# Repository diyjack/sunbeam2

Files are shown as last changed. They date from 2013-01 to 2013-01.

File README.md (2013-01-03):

##Sunbeam2.0
==========

##What is it?
Just a smoothieboard based electronics that im developing.

## Licensing
==========

Copyright (C) 2012 Arkadiusz Spiewak (Wulfnor)

licensed under the GPL license: [http://www.gnu.org/licenses/gpl.html](http://www.gnu.org/licenses/gpl.html)
license.txt file included.

##Author
Author is: Arkadiusz Spiewak a'ka Wulfnor

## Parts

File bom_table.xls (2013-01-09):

Count | Value | Package | Manufacturer number | Digikey number | Notes | Parts | Digikey link | Farnel
1 | 74LVC1G04 | SOT-353 | SN74LVC1G04DCKR | 296-11600-1-ND |  | U4 | http://www.digikey.com/product-detail/en/SN74LVC1G04DCKR/296-11600-1-ND/385739
5 | 100uF | CPOL-EUUD-6,3X7,7 | EEE-1VA101XP | PCE3951CT-ND | >=35V | C23, C33, C40, C47, C54 | http://www.digikey.com/product-detail/en/EEE-1VA101XP/PCE3951CT-ND/766327
3 | FERRITE | FERRITE_0603 | MMZ1608S601A | 445-1549-1-ND |  | FB1, FB2, FB3 | http://www.digikey.com/product-detail/en/MMZ1608S601A/445-1549-1-ND/571879
1 | 39nH | INDUCTOR0603 | 1-1624109-1 | A102551CT-ND |  | L2 | http://www.digikey.com/product-detail/en/1-1624109-1/A102551CT-ND/2728577
1 | LAN8720 | 24-VFQFN | LAN8720A-CP | 638-1080-ND |  | U3 | http://www.digikey.com/product-detail/en/LAN8720A-CP/638-1080-ND/2051556
4 | Red | LEDCHIPLED_0805 | APT2012EC | 754-1128-1-ND |  | LED6, LED7, LED8, RX | http://www.digikey.com/product-detail/en/APT2012EC/754-1128-1-ND/1747845
3 | Green | LEDCHIPLED_0805 | APT2012SGC | 754-1131-1-ND |  | 3V3, +5V, TX | http://www.digikey.com/product-detail/en/APT2012SGC/754-1131-1-ND/1747848
3 | Blue | LEDCHIPLED_0805 | APHCM2012QBC/D-F01 | 754-1505-1-ND |  | LED2, LED3, LED4 | http://www.digikey.com/product-detail/en/APHCM2012QBC%2FD-F01/754-1505-1-ND/2263579
1 | LPC1769 | 100-LQFP | LPC1769FBD100,551 | 568-4966-ND |  | LPC1769 | http://www.digikey.com/product-search/en/integrated-circuits-ics/embedded-microcontrollers/2556109?k=LPC1769
1 | IRLML2246TRPBF | SOT-23 | IRLML2246TRPBF | IRLML2246TRPBFCT-ND |  | T1 | http://www.digikey.com/product-detail/en/IRLML2246TRPBF/IRLML2246TRPBFCT-ND/2639576
3 |  | SWITCH_TACT_SMT | MJTP1140TR | 679-2328-1-ND |  | PLAY, PROGRAM, RESET | http://www.digikey.com/product-detail/en/MJTP1140TR/679-2328-1-ND/2344141
5 | .22uF | C-EUC0603 | C1608X7R1A224K | 445-5132-1-ND |  | C16, C24, C34, C41, C48 | http://www.digikey.com/product-detail/en/C1608X7R1A224K/445-5132-1-ND/2093747
24 | 0.1uF | C-EUC0603 | C1608X7R1E104K080AA | 445-1316-1-ND |  | C3, C4, C5, C6, C7, C8, C9, C10, C17, C19, C29, C36, C43, C50, C55, C57, C58, C59, C63, C72, C79, C82, C83, C84 | http://www.digikey.com/product-detail/en/C1608X7R1E104K080AA/445-1316-1-ND/567697
16 | 0.1uF | C-EUC0805 | C2012X7R1H104K085AA | 445-7534-1-ND |  | C15, C20, C21, C22, C30, C31, C32, C37, C38, C39, C44, C45, C46, C51, C52, C53 | http://www.digikey.com/product-detail/en/C2012X7R1H104K085AA/445-7534-1-ND/2733606
10 | 0.5R | R-EU_R2512 | MCS3264R050FER | MCS3264R050FERCT-ND | 2W, 1% | R12, R13, R29, R30, R37, R38, R45, R46, R53, R54 | http://www.digikey.com/product-detail/en/MCS3264R050FER/MCS3264R050FERCT-ND/2003884
5 | 1K | R-EU_R0603 | ERJ-3GEYJ102V | P1.0KGCT-ND |  | R4, R74, R75, R82, R91 | http://www.digikey.com/product-detail/en/ERJ-3GEYJ102V/P1.0KGCT-ND/134874
9 | 1K5 | R-EU_R0603 | ERJ-3GEYJ152V | P1.5KGCT-ND |  | R17, R19, R21, R57, R63, R73, R94, R95, R96 | http://www.digikey.com/product-detail/en/ERJ-3GEYJ152V/P1.5KGCT-ND/134974
1 | 1M | R-EU_R0603 | ERJ-3GEYJ105V | P1.0MGCT-ND |  | R62 | http://www.digikey.com/product-detail/en/ERJ-3GEYJ105V/P1.0MGCT-ND/134885
7 | 1uF | C-EUC0603 | C1608X5R0J105K | 445-1322-1-ND |  | C18, C28, C35, C42, C49, C70, C71 | http://www.digikey.com/product-detail/en/C1608X5R0J105K/445-1322-1-ND/567695
1 | 1uF | CAP_POL1206 | F931C105MAA | 493-2364-1-ND |  | C60 | http://www.digikey.com/product-detail/en/F931C105MAA/493-2364-1-ND/677832
2 | 4.7uF | C-EUC0603 | C1608Y5V0J475Z | 445-3449-1-ND |  | C85, C86 | http://www.digikey.com/product-detail/en/C1608Y5V0J475Z/445-3449-1-ND/1801548
4 | 4K7 | R-EU_R0603 | ERJ-3GEYJ472V | P4.7KGCT-ND |  | R22, R23, R24,R90 | http://www.digikey.com/product-detail/en/ERJ-3GEYJ472V/P4.7KGCT-ND/135199
46 | 10K | R-EU_R0603 | ERJ-3GEYJ103V | P10KGCT-ND |  | R5, R6, R7, R8, R9, R10, R14, R15, R16, R18, R20, R25, R26, R27, R31, R32, R33, R34, R35, R39, R40, R41, R42, R43, R47, R48, R49, R50, R51, R55, R56, R58, R70, R71, R72, R77, R79, R81, R83, R88, R89,R11, R28, R36, R44, R52 | http://www.digikey.com/product-detail/en/ERJ-3GEYJ103V/P10KGCT-ND/134717
1 | 10nF | C-EUC0805 | C2012X7R1H103K | 445-1348-1-ND |  | C77 | http://www.digikey.com/product-detail/en/C2012X7R1H103K/445-1348-1-ND/567641
3 | 10uF | C-EUC0603 | C1608X5R0J106M080AB | 445-4112-1-ND |  | C25, C26, C27 | http://www.digikey.com/product-detail/en/C1608X5R0J106M080AB/445-4112-1-ND/1975462
5 | 10uF | CAP_POL1206 | F931A106MAA | 493-2351-1-ND |  | C11, C14, C56, C61, C73 | http://www.digikey.com/product-detail/en/F931A106MAA/493-2351-1-ND/677819
1 | 12Mhz | CRYSTAL2734 | 403C35D12M00000 | CTX839CT-ND |  | U$3 | http://www.digikey.com/product-detail/en/403C35D12M00000/CTX839CT-ND/2293004
10 | 18pF | C-EUC0603 | C1608C0G1H180J080AA | 445-1272-1-ND |  | C1, C2, C12, C13, C64, C65, C66, C67, C68, C69 | http://www.digikey.com/product-detail/en/C1608C0G1H180J080AA/445-1272-1-ND/567674
6 | 22-23-2021 | 22-23-2021 | 22272021 | WM4111-ND |  | FAN1, FAN2, FAN3, T_E0, T_E1, T_HB | http://www.digikey.com/product-detail/en/0022272021/WM4111-ND/1130577
6 | 22-23-2031 | 22-23-2031 | 22272031 | WM4112-ND |  | X_MAX, X_MIN, Y_MAX, Y_MIN, Z_MAX, Z_MIN | http://www.digikey.com/product-detail/en/0022272031/WM4112-ND/1130578
5 | 22-23-2041 | 22-23-2041 | 22272041 | WM4113-ND |  | E0_AXIS, E1_AXIS, X_AXIS, Y_AXIS, Z_AXIS | http://www.digikey.com/product-detail/en/0022272041/WM4113-ND/1130579
6 | 22R | R-EU_R0603 | ERJ-3GEYJ220V | P22GCT-ND |  | R59, R60, R61, R76, R78, R80 | http://www.digikey.com/product-detail/en/ERJ-3GEYJ220V/P22GCT-ND/134662
1 | 25Mhz | CRYSTAL2734 | 403C35D25M00000 | CTX953CT-ND |  | U$8 | http://www.digikey.com/product-detail/en/403C35D25M00000/CTX953CT-ND/2640300
2 | 33R | R-EU_R0603 | ERJ-3GEYJ330V | P33GCT-ND |  | R1, R2 | http://www.digikey.com/product-detail/en/ERJ-3GEYJ330V/P33GCT-ND/134674
1 | 33uH | L-EUPIS2816 | 46333C | 811-1177-1-ND |  | L4 | http://www.digikey.com/product-detail/en/46333C/811-1177-1-ND/1924937
1 | 47uF | CAP_TANTALUMD/7343_REFLOW | TPSD476K016R0150 | 478-1788-1-ND |  | C76 | http://www.digikey.com/product-detail/en/TPSD476K016R0150/478-1788-1-ND/564820
4 | 49.9R | R-EU_R0603 | ERJ-3EKF49R9V | P49.9HCT-ND |  | R64, R65, R66, R67 | http://www.digikey.com/product-detail/en/ERJ-3EKF49R9V/P49.9HCT-ND/198412
1 | 470R | R-EU_R0603 | ERJ-3GEYJ471V | P470GCT-ND |  | R3 | http://www.digikey.com/product-detail/en/ERJ-3GEYJ471V/P470GCT-ND/134802
1 | 100uF | CPOL-EUUD-8X10 | EEE-FP1V101AP | PCE4442CT-ND |  | C78 | http://www.digikey.com/product-detail/en/EEE-FP1V101AP/PCE4442CT-ND/1246022
1 | 220uF | CPOL-EUUD-8X10 | ECE-V1AA221P | PCE2040CT-ND |  | C74 | http://www.digikey.com/product-detail/en/ECE-V1AA221P/PCE2040CT-ND/204211
2 | 330R | R-EU_R0603 | ERJ-3GEYJ331V | P330GCT-ND |  | R68, R69 | http://www.digikey.com/product-detail/en/ERJ-3GEYJ331V/P330GCT-ND/134778
1 | 470nF | C-EUC0805 | C2012Y5V1H474Z/0.85 | 445-7681-1-ND |  | C75 | http://www.digikey.com/product-detail/en/C2012Y5V1H474Z%2F0.85/445-7681-1-ND/2733753
1 | 470pF | C-EUC0603 | C1608X7R1H471K | 445-1307-1-ND |  | C62 | http://www.digikey.com/product-detail/en/C1608X7R1H471K/445-1307-1-ND/567709
2 | 500mA | L-EUL1812 | 0ZCC0050FF2C | 507-1361-1-ND |  | F1, F2 | http://www.digikey.com/product-detail/en/0ZCC0050FF2C/507-1361-1-ND/1560228
1 | 2520- | 2520- | 30320-6002HB | 3M11932-ND |  | PANEL | http://www.digikey.com/product-detail/en/30320-6002HB/3M11932-ND/1237399
5 | A4988 | 28-VFQFN | A4988SETTR-T | 620-1343-1-ND |  | IC2, IC3, IC4, IC5, IC6 | http://www.digikey.com/product-detail/en/A4988SETTR-T/620-1343-1-ND/2238004
1 | AD5206 | 24-TSSOP | AD5206BRUZ10-RL7 | AD5206BRUZ10-RL7CT-ND |  | AD5206 | http://www.digikey.com/product-detail/en/AD5206BRUZ10-RL7/AD5206BRUZ10-RL7CT-ND/3727008
1 | BC857ALT1SMD | SOT-23 | BC857A,215 | 568-6082-1-ND |  | Q1 | http://www.digikey.com/product-detail/en/BC857A,215/568-6082-1-ND/2531369
5 | Extruder0 | W237-102 | 1776244-2 | A97996-ND |  | E0, E1, HB, V_HEAT, V_MOT | http://www.digikey.com/product-detail/en/1776244-2/A97996-ND/1826859
1 | FT232RLSSOP | 28-SSOP | FT232RL-REEL | 768-1007-1-ND |  | IC7 | http://www.digikey.com/product-detail/en/FT232RL-REEL/768-1007-1-ND/1836402
1 | J0011D21B | J0011D21B | J0011D21BNL | 553-1485-ND |  | RJ1 | http://www.digikey.com/scripts/dksearch/dksus.dll?vendor=0&keywords=J0011D21B
3 | IRLHM630TR2PBF | PQFN (3x3) | RLHM630TR2PBF | IRLHM630TR2PBFCT-ND |  | Q2, Q3, Q4 | http://www.digikey.com/product-detail/en/IRLHM630TR2PBF/IRLHM630TR2PBFCT-ND/2464888
3 | IRLR8743 | D-Pak | IRLR8743TRPBF | IRLR8743TRPBFCT-ND |  | E0_FET, E1_FET, HOTBET_FET | http://www.digikey.com/product-detail/en/IRLR8743TRPBF/IRLR8743TRPBFCT-ND/1925566
1 | LM1117IMPX-3.3 | SOT-223-3 | LM1117MPX-3.3/NOPB | LM1117MPX-3.3/NOPBCT-ND |  | IC10 | http://www.digikey.com/product-detail/en/LM1117MPX-3.3%2FNOPB/LM1117MPX-3.3%2FNOPBCT-ND/1010516
1 | LM2675 | 8-SOIC | LM2675M-5.0/NOPB | LM2675M-5.0/NOPB-ND |  | IC8 | http://www.digikey.com/product-detail/en/LM2675M-5.0%2FNOPB/LM2675M-5.0%2FNOPB-ND/271162
1 | LMV358MMX | 8-MSOP | LMV358MM/NOPB | LMV358MM/NOPBCT-ND |  | IC9 | http://www.digikey.com/product-detail/en/LMV358MM%2FNOPB/LMV358MM%2FNOPBCT-ND/270768
2 | M4 | DIODE-DO214AC | S1G-E3/5AT | S1G-E3/5ATGICT-ND |  | D2, D3 | http://www.digikey.com/product-detail/en/S1G-E3%2F5AT/S1G-E3%2F5ATGICT-ND/3025911
2 | SMF_OMNIBLOK_154.062 | SMF_OMNIBLOK_154.062 | 0154007.DR | F1229CT-ND |  | F3 | http://www.digikey.com/product-detail/en/0154007.DR/F1229CT-ND/565517
1 | 01530008Z | 01530008Z | 01530008Z | F065-ND |  | F4 | http://www.digikey.com/product-detail/en/01530008Z/F065-ND/183334
1 | SS14 | DIODE-DO214AC | SS14-E3/61T | SS14-E3/61TGICT-ND |  | D1 | http://www.digikey.com/product-detail/en/SS14-E3%2F61T/SS14-E3%2F61TGICT-ND/1091668
2 | TC4427 | 8-SOIC | TC4427ACOA713 | TC4427ACOA713CT-ND |  | FET_DRV1, FET_DRV2 | http://www.digikey.com/product-detail/en/TC4427ACOA713/TC4427ACOA713CT-ND/3622383
1 | USB+SHIELD | USB+SHIELD | 670689000 | WM17131-ND |  | U$1 | http://www.digikey.com/product-detail/en/0670689000/WM17131-ND/755221
1 | USB-MINIB-5PIN | USB-MINIB-5PIN | 675031020 | WM5461CT-ND |  | U$7 | http://www.digikey.com/product-detail/en/0675031020/WM5461CT-ND/1624427
1 | USD-SOCKETNEW | USD-SOCKETNEW | 101-00660-68-6 | 101-00660-68-6-1-ND |  | U2 | http://www.digikey.com/product-detail/en/101-00660-68-6/101-00660-68-6-1-ND/2187099
2 | VARISTORCN0603 | VARISTORCN0603 | B72500D50A60 | 495-3414-1-ND |  | R97, R98 | http://www.digikey.com/product-detail/en/B72500D50A60/495-3414-1-ND/1589665

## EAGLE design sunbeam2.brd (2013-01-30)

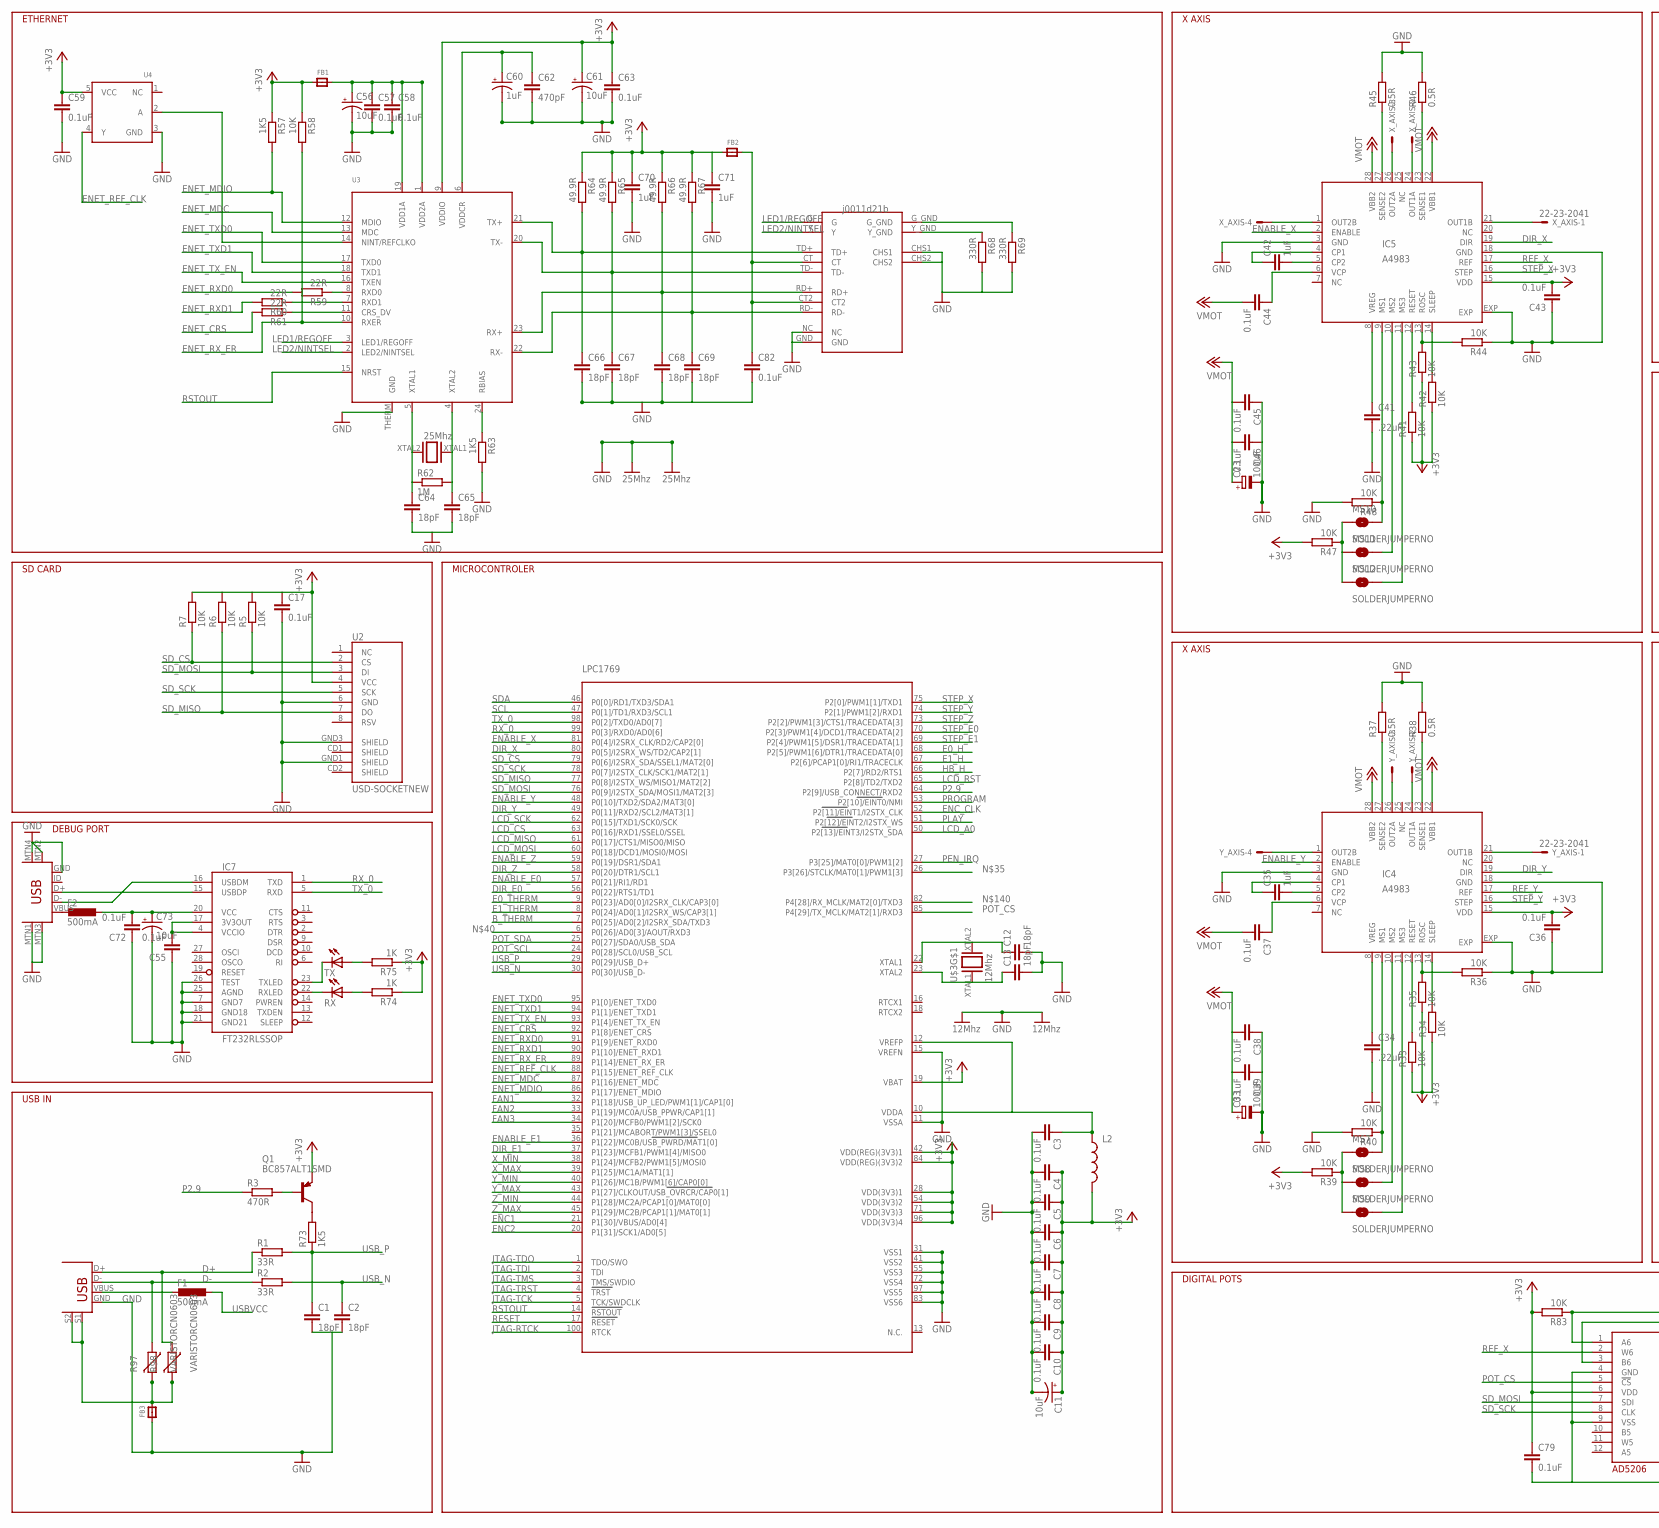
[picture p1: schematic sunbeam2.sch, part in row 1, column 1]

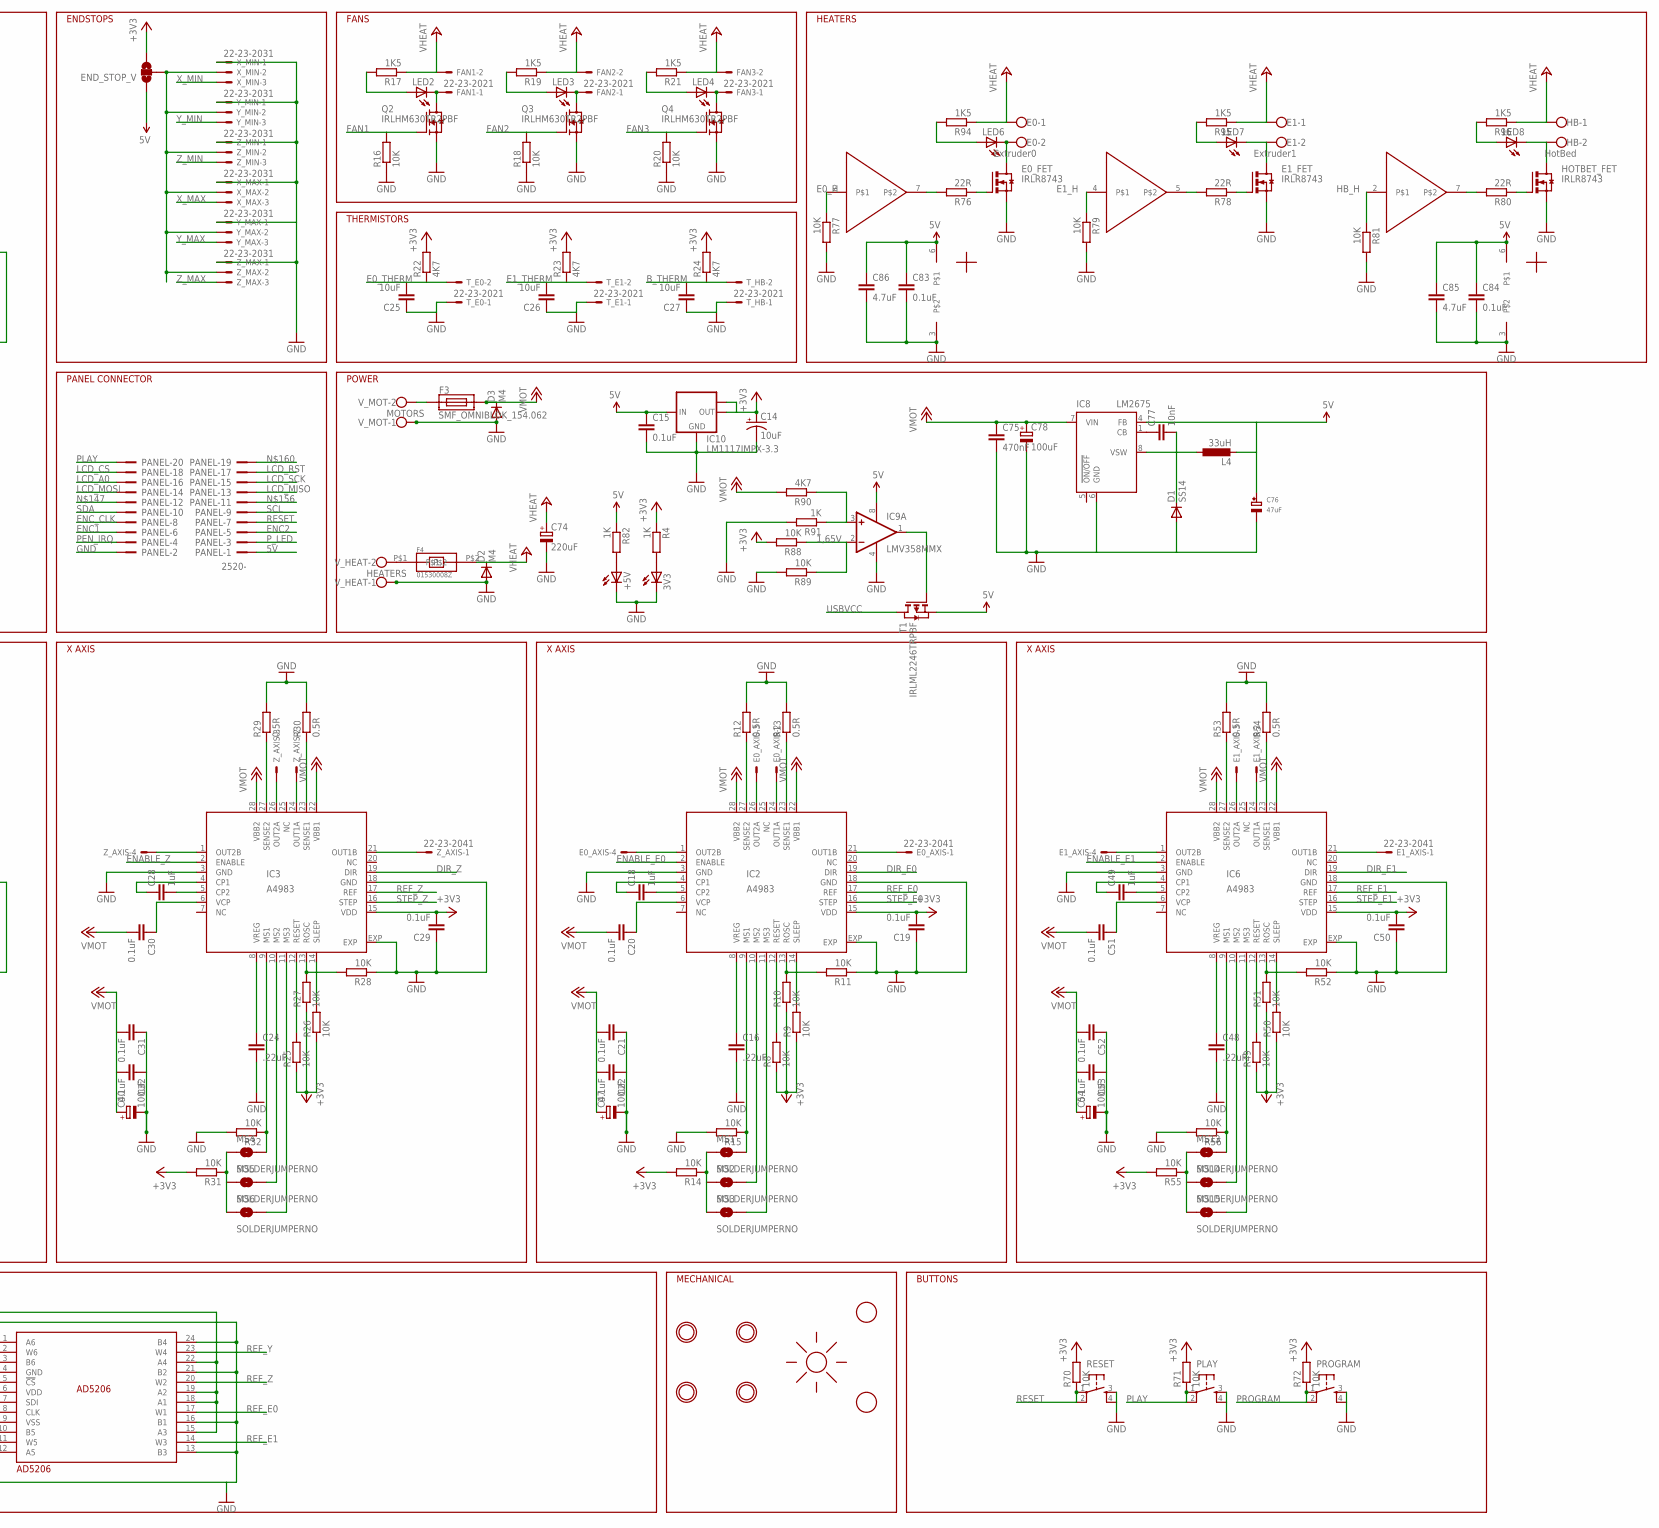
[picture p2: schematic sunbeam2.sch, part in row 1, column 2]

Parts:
3V3: LEDCHIPLED_0805; CHIPLED_0805
+5V: LEDCHIPLED_0805; CHIPLED_0805
AD5206: AD5206; TSSOP24
C1, C2, C12, C13, C64, C65, C66, C67, C68, C69: 18pF; C0603
C3, C4, C5, C6, C7, C8, C9, C10, C17, C19, C29, C36, C43, C50, C55, C57, C58, C59, C63, C72, C79, C82, C83, C84: 0.1uF; C0603
C11, C14, C56, C61, C73: 10uF; EIA3216
C15, C20, C21, C22, C30, C31, C32, C37, C38, C39, C44, C45, C46, C51, C52, C53: 0.1uF; C0805
C16, C24, C34, C41, C48: .22uF; C0603
C18, C28, C35, C42, C49, C70, C71: 1uF; C0603
C23, C33, C40, C47, C54: 100uF; UD-6,3X7,7_NICHICON
C25, C26, C27: 10uF; C0603
C60: 1uF; EIA3216
C62: 470pF; C0603
C74: 220uF; UD-8X10_NICHICON
C75: 470nF; C0805
C76: 47uF; EIA7343-31/D-R
C77: 10nF; C0805
C78: 100uF; UD-8X10_NICHICON
C85, C86: 4.7uF; C0603
D1: SS14; DO214AC
D2, D3: M4; DO214AC
E0: Extruder0; W237-102; MPN 237-102
E0_AXIS, E1_AXIS: 22-23-2041
E0_FET, E1_FET: IRLR8743; D-PAK_TO252AA
E1: Extruder1; W237-102; MPN 237-102
END_STOP_V: SOLDERJUMPER_2WAYS; SJ_3
F1, F2: 500mA; L1812
F3: SMF_OMNIBLOK_154.062; NANO2_SMF_FUSEBLOCK
F4: 01530008Z
FAN1, FAN2, FAN3: 22-23-2021
FB1, FB2, FB3: FERRITE_0603; _0603
FET_DRV1, FET_DRV2: TC4427; SOIC8
GND: MOUNTINGHOLE3.0THIN; MOUNTINGHOLE_3.0_PLATEDTHIN
HB: HotBed; W237-102; MPN 237-102
HOTBET_FET: IRLR8743; D-PAK_TO252AA
IC2, IC3, IC4, IC5, IC6: A4983; QFN28ET
IC7: FT232RLSSOP; SSOP28DB
IC8: LM2675; SO08
IC9: LMV358MMX; MSOP08
IC10: LM1117IMPX-3.3; SOT223
L2: INDUCTOR0603; 0603
L4: 33uH; PIS2816
LED2, LED3, LED4, LED6, LED7, LED8: LEDCHIPLED_0805; CHIPLED_0805
LPC1769: LPC1768; LQFP100
MS1, MS2, MS3, MS4, MS5, MS6, MS7, MS8, MS9, MS10, MS11, MS12, MS13, MS14, MS15: SOLDERJUMPERNO; SJ_2S-NO
PANEL: 2520-; PAK100/2500-20
PLAY: TAC_SWITCHSMD; TACTILE_SWITCH_SMD
PROGRAM: TAC_SWITCHSMD; TACTILE_SWITCH_SMD
Q1: BC857ALT1SMD; SOT23-BEC
Q2, Q3, Q4: IRLHM630TR2PBF; PQFN33
R1, R2: 33R; R0603
R3: 470R; R0603
R4, R74, R75, R82, R91: 1K; R0603
R5, R6, R7, R8, R9, R10, R11, R14, R15, R16, R18, R20, R25, R26, R27, R28, R31, R32, R33, R34, R35, R36, R39, R40, R41, R42, R43, R44, R47, R48, R49, R50, R51, R52, R55, R56, R58, R70, R71, R72, R77, R79, R81, R83, R88, R89: 10K; R0603
R12, R13, R29, R30, R37, R38, R45, R46, R53, R54: 0.5R; R2512
R17, R19, R21, R57, R63, R73, R94, R95, R96: 1K5; R0603
R22, R23, R24, R90: 4K7; R0603
R59, R60, R61, R76, R78, R80: 22R; R0603
R62: 1M; R0603
R64, R65, R66, R67: 49.9R; R0603
R68, R69: 330R; R0603
R97, R98: VARISTORCN0603; CT/CN0603
RESET: TAC_SWITCHSMD; TACTILE_SWITCH_SMD
RJ1: ETHERNET; J0011D21B
RX: LEDCHIPLED_0805; CHIPLED_0805
T1: IRLML2246TRPBF; SOT-23
TX: LEDCHIPLED_0805; CHIPLED_0805
T_E0, T_E1: 22-23-2021
T_HB: 22-23-2021
U2: USD-SOCKETNEW; MICRO-SD-SOCKET-PP
U3: LAN8720; QFN24_4MM
U4: 74LVC1G04; SOT23-5
U$1: USB+SHIELD; USB-B-PTH
U$3: 12Mhz; CRYSTAL2734
U$7: USB-MINIB-5PIN; USB-MINIB
U$8: 25Mhz; CRYSTAL2734
U$17, U$18, U$20: MOUNTINGHOLE3.0THIN; MOUNTINGHOLE_3.0_PLATEDTHIN
U$21: SUNLOGO; SUN
U$22, U$23: FIDUCIAL; FIDUCIAL_1MM
V_HEAT: HEATERS; W237-102
V_MOT: MOTORS; W237-102
X_AXIS: 22-23-2041
X_MAX: 22-23-2031; MPN 22-23-2031
X_MIN: 22-23-2031
Y_AXIS: 22-23-2041
Y_MAX: 22-23-2031; MPN 22-23-2031
Y_MIN: 22-23-2031
Z_AXIS: 22-23-2041
Z_MAX: 22-23-2031; MPN 22-23-2031
Z_MIN: 22-23-2031

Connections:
1,65V: IC9.2 (-IN), R88.1, R89.1
5V: C15.1, C76.+, C83.1, C84.1, C85.1, C86.1, END_STOP_V.1, FET_DRV1.6, FET_DRV2.6, IC8.4 (FB), IC9.8 (V+), IC10.3 (IN), L4.2, PANEL.1, R82.1, T1.2 (S)
+3V3: AD5206.6 (VDD), C4.1, C5.1, C6.1, C7.1, C8.1, C9.1, C10.1, C11.A (+), C14.A (+), C17.1, C19.2, C29.2, C36.2, C43.2, C50.2, C59.1, C61.A (+), C63.1, C70.1, C71.1, C79.1, END_STOP_V.3, FB1.1, FB2.1, IC2.15 (VDD), IC3.15 (VDD), IC4.15 (VDD), IC5.15 (VDD), IC6.15 (VDD), IC10.2 (OUT), IC10.TAB (OUT1), L2.2, LPC1769.19 (VBAT), LPC1769.28 (VDD(3V3)1), LPC1769.42 (VDD(REG)(3V3)1), LPC1769.54 (VDD(3V3)2), LPC1769.71 (VDD(3V3)3), LPC1769.84 (VDD(REG)(3V3)2), LPC1769.96 (VDD(3V3)4), Q1.E, R4.1, R5.2, R6.2, R7.2, R8.1, R9.1, R10.1, R14.2, R22.2, R23.2, R24.2, R25.1, R26.1, R27.1, R31.2, R33.1, R34.1, R35.1, R39.2, R41.1, R42.1, R43.1, R47.2, R49.1, R50.1, R51.1, R55.2, R57.1, R58.1, R64.1, R65.1, R66.1, R67.1, R70.2, R71.2, R72.2, R74.1, R75.1, R83.2, R88.2, U2.4 (VCC), U3.9 (VDDIO), U4.5 (VCC)
+12V: C20.2, C21.2, C22.2, C23.+, C30.2, C31.2, C32.2, C33.+, C37.2, C38.2, C39.2, C40.+, C44.2, C45.2, C46.2, C47.+, C51.2, C52.2, C53.2, C54.+, C75.1, C78.+, D3.C, F3.2, IC2.22 (VBB1), IC2.28 (VBB2), IC3.22 (VBB1), IC3.28 (VBB2), IC4.22 (VBB1), IC4.28 (VBB2), IC5.22 (VBB1), IC5.28 (VBB2), IC6.22 (VBB1), IC6.28 (VBB2), IC8.7 (VIN), R90.2
B_THERM: C27.2, LPC1769.7 (P0[25]/AD0[2]/I2SRX_SDA/TXD3), R24.1, T_HB.2
D+: R1.1, R98.1, U$1.D+
D-: R2.1, R97.1, U$1.D-
DIR_E0: IC2.19 (DIR), LPC1769.56 (P0[22]/RTS1/TD1)
DIR_E1: IC6.19 (DIR), LPC1769.37 (P1[23]/MCFB1/PWM1[4]/MISO0)
DIR_X: IC5.19 (DIR), LPC1769.80 (P0[5]/I2SRX_WS/TD2/CAP2[1])
DIR_Y: IC4.19 (DIR), LPC1769.49 (P0[11]/RXD2/SCL2/MAT3[1])
DIR_Z: IC3.19 (DIR), LPC1769.58 (P0[20]/DTR1/SCL1)
E0_H: FET_DRV1.2, LPC1769.68 (P2[5]/PWM1[6]/DTR1/TRACEDATA[0]), R77.1
E0_THERM: C25.2, LPC1769.9 (P0[23]/AD0[0]/I2SRX_CLK/CAP3[0]), R22.1, T_E0.2
E1_H: FET_DRV1.4, LPC1769.67 (P2[6]/PCAP1[0]/RI1/TRACECLK), R79.1
E1_THERM: C26.2, LPC1769.8 (P0[24]/AD0[1]/I2SRX_WS/CAP3[1]), R23.1, T_E1.2
ENABLE_E0: IC2.2 (ENABLE), LPC1769.57 (P0[21]/RI1/RD1)
ENABLE_E1: IC6.2 (ENABLE), LPC1769.36 (P1[22]/MC0B/USB_PWRD/MAT1[0])
ENABLE_X: IC5.2 (ENABLE), LPC1769.81 (P0[4]/I2SRX_CLK/RD2/CAP2[0])
ENABLE_Y: IC4.2 (ENABLE), LPC1769.48 (P0[10]/TXD2/SDA2/MAT3[0])
ENABLE_Z: IC3.2 (ENABLE), LPC1769.59 (P0[19]/DSR1/SDA1)
ENC1: LPC1769.21 (P1[30]/VBUS/AD0[4]), PANEL.6
ENC2: LPC1769.20 (P1[31]/SCK1/AD0[5]), PANEL.5
ENC_CLK: LPC1769.52 (P2[11]/EINT1/I2STX_CLK), PANEL.8
ENET_CRS: LPC1769.92 (P1[8]/ENET_CRS), R61.2
ENET_MDC: LPC1769.87 (P1[16]/ENET_MDC), U3.13 (MDC)
ENET_MDIO: LPC1769.86 (P1[17]/ENET_MDIO), R57.2, U3.12 (MDIO)
ENET_REF_CLK: LPC1769.88 (P1[15]/ENET_REF_CLK), U4.4 (Y)
ENET_RXD0: LPC1769.91 (P1[9]/ENET_RXD0), R59.2
ENET_RXD1: LPC1769.90 (P1[10]/ENET_RXD1), R60.2
ENET_RX_ER: LPC1769.89 (P1[14]/ENET_RX_ER), R58.2, U3.10 (RXER)
ENET_TXD0: LPC1769.95 (P1[0]/ENET_TXD0), U3.17 (TXD0)
ENET_TXD1: LPC1769.94 (P1[1]/ENET_TXD1), U3.18 (TXD1)
ENET_TX_EN: LPC1769.93 (P1[4]/ENET_TX_EN), U3.16 (TXEN)
FAN1: LPC1769.32 (P1[18]/USB_UP_LED/PWM1[1]/CAP1[0]), Q2.G, R16.2
FAN2: LPC1769.33 (P1[19]/MC0A/USB_PPWR/CAP1[1]), Q3.G, R18.2
FAN3: LPC1769.34 (P1[20]/MCFB0/PWM1[2]/SCK0), Q4.G, R20.2
GND: 3V3.C, +5V.C, AD5206.3 (B6), AD5206.4 (GND), AD5206.9 (VSS), AD5206.13 (B3), AD5206.16 (B1), AD5206.21 (B2), AD5206.24 (B4), C1.2, C2.2, C3.2, C4.2, C5.2, C6.2, C7.2, C8.2, C9.2, C10.2, C11.C (-), C12.2, C13.2, C14.C (-), C15.2, C16.2, C17.2, C19.1, C21.1, C22.1, C23.-, C24.2, C25.1, C26.1, C27.1, C29.1, C31.1, C32.1, C33.-, C34.2, C36.1, C38.1, C39.1, C40.-, C41.2, C43.1, C45.1, C46.1, C47.-, C48.2, C50.1, C52.1, C53.1, C54.-, C55.1, C56.C (-), C57.2, C58.2, C59.2, C60.C (-), C61.C (-), C62.2, C63.2, C64.2, C65.2, C66.2, C67.2, C68.2, C69.2, C70.2, C71.2, C72.1, C73.C (-), C74.-, C75.2, C76.-, C78.-, C79.2, C82.2, C83.2, C84.2, C85.2, C86.2, D1.A, D2.A, D3.A, E0_FET.3 (S), E1_FET.3 (S), FB3.1, FET_DRV1.3, FET_DRV2.3, HOTBET_FET.3 (S), IC2.3 (GND), IC2.18 (GND), IC2.EXP, IC3.3 (GND), IC3.18 (GND), IC3.EXP, IC4.3 (GND), IC4.18 (GND), IC4.EXP, IC5.3 (GND), IC5.18 (GND), IC5.EXP, IC6.3 (GND), IC6.18 (GND), IC6.EXP, IC7.7 (GND7), IC7.18 (GND18), IC7.21 (GND21), IC7.25 (AGND), IC7.26 (TEST), IC8.6 (GND), IC9.4 (V-), IC10.1 (GND), LPC1769.11 (VSSA), LPC1769.15 (VREFN), LPC1769.31 (VSS1), LPC1769.41 (VSS2), LPC1769.55 (VSS3), LPC1769.72 (VSS4), LPC1769.83 (VSS6), LPC1769.97 (VSS5), PANEL.2, PLAY.3, PLAY.4, PROGRAM.3, PROGRAM.4, Q2.S, Q3.S, Q4.S, R11.1, R12.2, R13.2, R15.2, R16.1, R18.1, R20.1, R28.1, R29.2, R30.2, R32.2, R36.1, R37.2, R38.2, R40.2, R44.1, R45.2, R46.2, R48.2, R52.1, R53.2, R54.2, R56.2, R63.2, R68.2, R69.2, R77.2, R79.2, R81.2, R89.2, R91.2, RESET.3, RESET.4, RJ1.CHS1, RJ1.CHS2, RJ1.GND, RJ1.NC, T_E0.1, T_E1.1, T_HB.1, U2.6 (GND), U2.GND1 (SHIELD), U2.GND3 (SHIELD), U3.THERM (GND), U4.3 (GND), U$1.GND, U$3.GND1 (GND), U$3.GND2 (GND), U$7.GND, U$7.MTN1 (MTN2), U$7.MTN2 (MTN3), U$7.MTN3 (MTN1), U$7.MTN4, U$8.GND1 (GND), U$8.GND2 (GND), V_HEAT.1, V_MOT.1, X_MAX.1, X_MIN.1, Y_MAX.1, Y_MIN.1, Z_MAX.1, Z_MIN.1
HB_H: FET_DRV2.2, LPC1769.66 (P2[7]/RD2/RTS1), R81.1
JTAG-RTCK: LPC1769.100 (RTCK)
JTAG-TCK: LPC1769.5 (TCK/SWDCLK)
JTAG-TDI: LPC1769.2 (TDI)
JTAG-TDO: LPC1769.1 (TDO/SWO)
JTAG-TMS: LPC1769.3 (TMS/SWDIO)
JTAG-TRST: LPC1769.4 (TRST)
LCD_A0: LPC1769.50 (P2[13]/EINT3/I2STX_SDA), PANEL.16
LCD_CS: LPC1769.63 (P0[16]/RXD1/SSEL0/SSEL), PANEL.18
LCD_MISO: LPC1769.61 (P0[17]/CTS1/MISO0/MISO), PANEL.13
LCD_MOSI: LPC1769.60 (P0[18]/DCD1/MOSI0/MOSI), PANEL.14
LCD_RST: LPC1769.65 (P2[8]/TD2/TXD2), PANEL.17
LCD_SCK: LPC1769.62 (P0[15]/TXD1/SCK0/SCK), PANEL.15
LED1/REGOFF: RJ1.G, U3.3 (LED1/REGOFF)
LED2/NINTSEL: RJ1.Y, U3.2 (LED2/NINTSEL)
unnamed: F1.2, U$1.VBUS
unnamed: Q1.B, R3.2
unnamed: FB3.2, R97.2, R98.2, U$1.S1, U$1.S2
unnamed: FAN1.1, LED2.C, Q2.D
unnamed: FAN2.1, LED3.C, Q3.D
unnamed: C13.1, LPC1769.23 (XTAL2), U$3.XTAL1 (1)
unnamed: C12.1, LPC1769.22 (XTAL1), U$3.XTAL2 (2)
unnamed: E0_AXIS.1, IC2.21 (OUT1B)
unnamed: E0_AXIS.2, IC2.24 (OUT1A)
unnamed: 3V3.A, R4.2
unnamed: C3.1, L2.1, LPC1769.10 (VDDA), LPC1769.12 (VREFP)
unnamed: E0_AXIS.3, IC2.26 (OUT2A)
unnamed: E0_AXIS.4, IC2.1 (OUT2B)
unnamed: IC2.12 (RESET), R8.2
unnamed: IC2.14 (SLEEP), R9.2
unnamed: IC2.13 (ROSC), R10.2, R11.2
unnamed: C16.1, IC2.8 (VREG)
unnamed: C18.2, IC2.5 (CP2)
unnamed: C18.1, IC2.4 (CP1)
unnamed: IC2.27 (SENSE2), R12.1
unnamed: IC2.23 (SENSE1), R13.1
unnamed: C20.1, IC2.6 (VCP)
unnamed: IC2.9 (MS1), MS1.2, R15.1
unnamed: IC2.10 (MS2), MS2.2
unnamed: IC2.11 (MS3), MS3.2
unnamed: MS1.1, MS2.1, MS3.1, R14.1
unnamed: F3.1, V_MOT.2
unnamed: HB.2, HOTBET_FET.4 (D), LED8.C
unnamed: E1.2, E1_FET.4 (D), LED7.C
unnamed: E0.2, E0_FET.4 (D), LED6.C
unnamed: E0_FET.1 (G), R76.1
unnamed: E1_FET.1 (G), R78.1
unnamed: FET_DRV1.7, R76.2
unnamed: LED6.A, R94.2
unnamed: Q1.C, R73.2
unnamed: IC3.21 (OUT1B), Z_AXIS.1
unnamed: IC3.24 (OUT1A), Z_AXIS.2
unnamed: IC3.26 (OUT2A), Z_AXIS.3
unnamed: IC3.1 (OUT2B), Z_AXIS.4
unnamed: LED3.A, R19.2
unnamed: END_STOP_V.2, X_MAX.2, X_MIN.2, Y_MAX.2, Y_MIN.2, Z_MAX.2, Z_MIN.2
unnamed: LED2.A, R17.2
unnamed: FAN3.1, LED4.C, Q4.D
unnamed: LED4.A, R21.2
unnamed: IC3.12 (RESET), R25.2
unnamed: IC3.14 (SLEEP), R26.2
unnamed: IC3.13 (ROSC), R27.2, R28.2
unnamed: C24.1, IC3.8 (VREG)
unnamed: C28.2, IC3.5 (CP2)
unnamed: C28.1, IC3.4 (CP1)
unnamed: IC3.27 (SENSE2), R29.1
unnamed: IC3.23 (SENSE1), R30.1
unnamed: C30.1, IC3.6 (VCP)
unnamed: IC3.9 (MS1), MS4.2, R32.1
unnamed: IC3.10 (MS2), MS5.2
unnamed: IC3.11 (MS3), MS6.2
unnamed: MS4.1, MS5.1, MS6.1, R31.1
unnamed: IC4.21 (OUT1B), Y_AXIS.1
unnamed: IC4.24 (OUT1A), Y_AXIS.2
unnamed: IC4.26 (OUT2A), Y_AXIS.3
unnamed: IC4.1 (OUT2B), Y_AXIS.4
unnamed: IC4.12 (RESET), R33.2
unnamed: IC4.14 (SLEEP), R34.2
unnamed: IC4.13 (ROSC), R35.2, R36.2
unnamed: C34.1, IC4.8 (VREG)
unnamed: C35.2, IC4.5 (CP2)
unnamed: C35.1, IC4.4 (CP1)
unnamed: IC4.27 (SENSE2), R37.1
unnamed: IC4.23 (SENSE1), R38.1
unnamed: C37.1, IC4.6 (VCP)
unnamed: IC4.9 (MS1), MS7.2, R40.1
unnamed: IC4.10 (MS2), MS8.2
unnamed: IC4.11 (MS3), MS9.2
unnamed: MS7.1, MS8.1, MS9.1, R39.1
unnamed: IC5.21 (OUT1B), X_AXIS.1
unnamed: IC5.24 (OUT1A), X_AXIS.2
unnamed: IC5.26 (OUT2A), X_AXIS.3
unnamed: IC5.1 (OUT2B), X_AXIS.4
unnamed: IC5.12 (RESET), R41.2
unnamed: IC5.14 (SLEEP), R42.2
unnamed: IC5.13 (ROSC), R43.2, R44.2
unnamed: C41.1, IC5.8 (VREG)
unnamed: C42.2, IC5.5 (CP2)
unnamed: C42.1, IC5.4 (CP1)
unnamed: IC5.27 (SENSE2), R45.1
unnamed: IC5.23 (SENSE1), R46.1
unnamed: C44.1, IC5.6 (VCP)
unnamed: IC5.9 (MS1), MS10.2, R48.1
unnamed: IC5.10 (MS2), MS11.2
unnamed: IC5.11 (MS3), MS12.2
unnamed: MS10.1, MS11.1, MS12.1, R47.1
unnamed: E1_AXIS.1, IC6.21 (OUT1B)
unnamed: E1_AXIS.2, IC6.24 (OUT1A)
unnamed: E1_AXIS.3, IC6.26 (OUT2A)
unnamed: E1_AXIS.4, IC6.1 (OUT2B)
unnamed: IC6.12 (RESET), R49.2
unnamed: IC6.14 (SLEEP), R50.2
unnamed: IC6.13 (ROSC), R51.2, R52.2
unnamed: C48.1, IC6.8 (VREG)
unnamed: C49.2, IC6.5 (CP2)
unnamed: C49.1, IC6.4 (CP1)
unnamed: IC6.27 (SENSE2), R53.1
unnamed: IC6.23 (SENSE1), R54.1
unnamed: C51.1, IC6.6 (VCP)
unnamed: IC6.9 (MS1), MS13.2, R56.1
unnamed: IC6.10 (MS2), MS14.2
unnamed: IC6.11 (MS3), MS15.2
unnamed: MS13.1, MS14.1, MS15.1, R55.1
unnamed: F2.2, U$7.VBUS
unnamed: IC7.15 (USBDP), U$7.D+
unnamed: IC7.16 (USBDM), U$7.D-
unnamed: C72.2, C73.A (+), F2.1, IC7.20 (VCC)
unnamed: C55.2, IC7.4 (VCCIO), IC7.17 (3V3OUT)
unnamed: IC7.22 (RXLED), RX.C
unnamed: F4.P$1, V_HEAT.2
unnamed: C56.A (+), C57.1, C58.1, FB1.2, U3.1 (VDD2A), U3.19 (VDD1A)
unnamed: R63.1, U3.24 (RBIAS)
unnamed: R74.2, RX.A
unnamed: U3.14 (NINT/REFCLKO), U4.2 (A)
unnamed: R59.1, U3.8 (RXD0)
unnamed: R60.1, U3.7 (RXD1)
unnamed: R61.1, U3.11 (CRS_DV)
unnamed: C65.1, R62.2, U3.4 (XTAL2), U$8.XTAL1 (1)
unnamed: C66.1, R64.2, RJ1.TD+, U3.21 (TX+)
unnamed: C60.A (+), C62.1, U3.6 (VDDCR)
unnamed: C64.1, R62.1, U3.5 (XTAL1), U$8.XTAL2 (2)
unnamed: C67.1, R65.2, RJ1.TD-, U3.20 (TX-)
unnamed: IC7.23 (TXLED), TX.C
unnamed: R75.2, TX.A
unnamed: FET_DRV1.5, R78.2
unnamed: C77.2, D1.C, IC8.8 (VSW), L4.1
unnamed: +5V.A, R82.2
unnamed: HOTBET_FET.1 (G), R80.1
unnamed: FET_DRV2.7, R80.2
unnamed: C69.1, R67.2, RJ1.RD-, U3.22 (RX-)
unnamed: LED7.A, R95.2
unnamed: C77.1, IC8.1 (CB)
unnamed: LED8.A, R96.2
unnamed: C68.1, R66.2, RJ1.RD+, U3.23 (RX+)
unnamed: AD5206.1 (A6), AD5206.15 (A3), AD5206.18 (A1), AD5206.19 (A2), AD5206.22 (A4), R83.1
unnamed: R68.1, RJ1.Y_GND
unnamed: R69.1, RJ1.G_GND
unnamed: C82.1, FB2.2, RJ1.CT, RJ1.CT2
unnamed: IC9.1 (OUT), T1.3 (G)
unnamed: IC9.3 (+IN), R90.1, R91.1
P2.9: LPC1769.64 (P2[9]/USB_CONNECT/RXD2), R3.1
PEN_IRQ: LPC1769.27 (P3[25]/MAT0[0]/PWM1[2]), PANEL.4
PLAY: LPC1769.51 (P2[12]/EINT2/I2STX_WS), PANEL.20, PLAY.1, PLAY.2, R71.1
POT_CS: AD5206.5 (!CS), LPC1769.85 (P4[29]/TX_MCLK/MAT2[1]/RXD3)
POT_SCL: LPC1769.24 (P0[28]/SCL0/USB_SCL)
POT_SDA: LPC1769.25 (P0[27]/SDA0/USB_SDA)
PROGRAM: LPC1769.53 (P2[10]/EINT0/NMI), PROGRAM.1, PROGRAM.2, R72.1
P_LED: PANEL.3
REF_E0: AD5206.17 (W1), IC2.17 (REF)
REF_E1: AD5206.14 (W3), IC6.17 (REF)
REF_X: AD5206.2 (W6), IC5.17 (REF)
REF_Y: AD5206.23 (W4), IC4.17 (REF)
REF_Z: AD5206.20 (W2), IC3.17 (REF)
RESET: LPC1769.17 (RESET), PANEL.7, R70.1, RESET.1, RESET.2
RSTOUT: LPC1769.14 (RSTOUT), U3.15 (NRST)
RX_0: IC7.1 (TXD), LPC1769.99 (P0[3]/RXD0/AD0[6])
SCL: LPC1769.47 (P0[1]/TD1/RXD3/SCL1), PANEL.9
SDA: LPC1769.46 (P0[0]/RD1/TXD3/SDA1), PANEL.10
SD_CS: LPC1769.79 (P0[6]/I2SRX_SDA/SSEL1/MAT2[0]), R7.1, U2.2 (CS)
SD_MISO: LPC1769.77 (P0[8]/I2STX_WS/MISO1/MAT2[2]), R6.1, U2.7 (DO)
SD_MOSI: AD5206.7 (SDI), LPC1769.76 (P0[9]/I2STX_SDA/MOSI1/MAT2[3]), R5.1, U2.3 (DI)
SD_SCK: AD5206.8 (CLK), LPC1769.78 (P0[7]/I2STX_CLK/SCK1/MAT2[1]), U2.5 (SCK)
STEP_E0: IC2.16 (STEP), LPC1769.70 (P2[3]/PWM1[4]/DCD1/TRACEDATA[2])
STEP_E1: IC6.16 (STEP), LPC1769.69 (P2[4]/PWM1[5]/DSR1/TRACEDATA[1])
STEP_X: IC5.16 (STEP), LPC1769.75 (P2[0]/PWM1[1]/TXD1)
STEP_Y: IC4.16 (STEP), LPC1769.74 (P2[1]/PWM1[2]/RXD1)
STEP_Z: IC3.16 (STEP), LPC1769.73 (P2[2]/PWM1[3]/CTS1/TRACEDATA[3])
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

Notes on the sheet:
USB IN
POWER
SD CARD
ETHERNET
ENDSTOPS
FANS
THERMISTORS
PANEL CONNECTOR
HEATERS
DEBUG PORT
X AXIS
MICROCONTROLER
DIGITAL POTS
MECHANICAL
BUTTONS

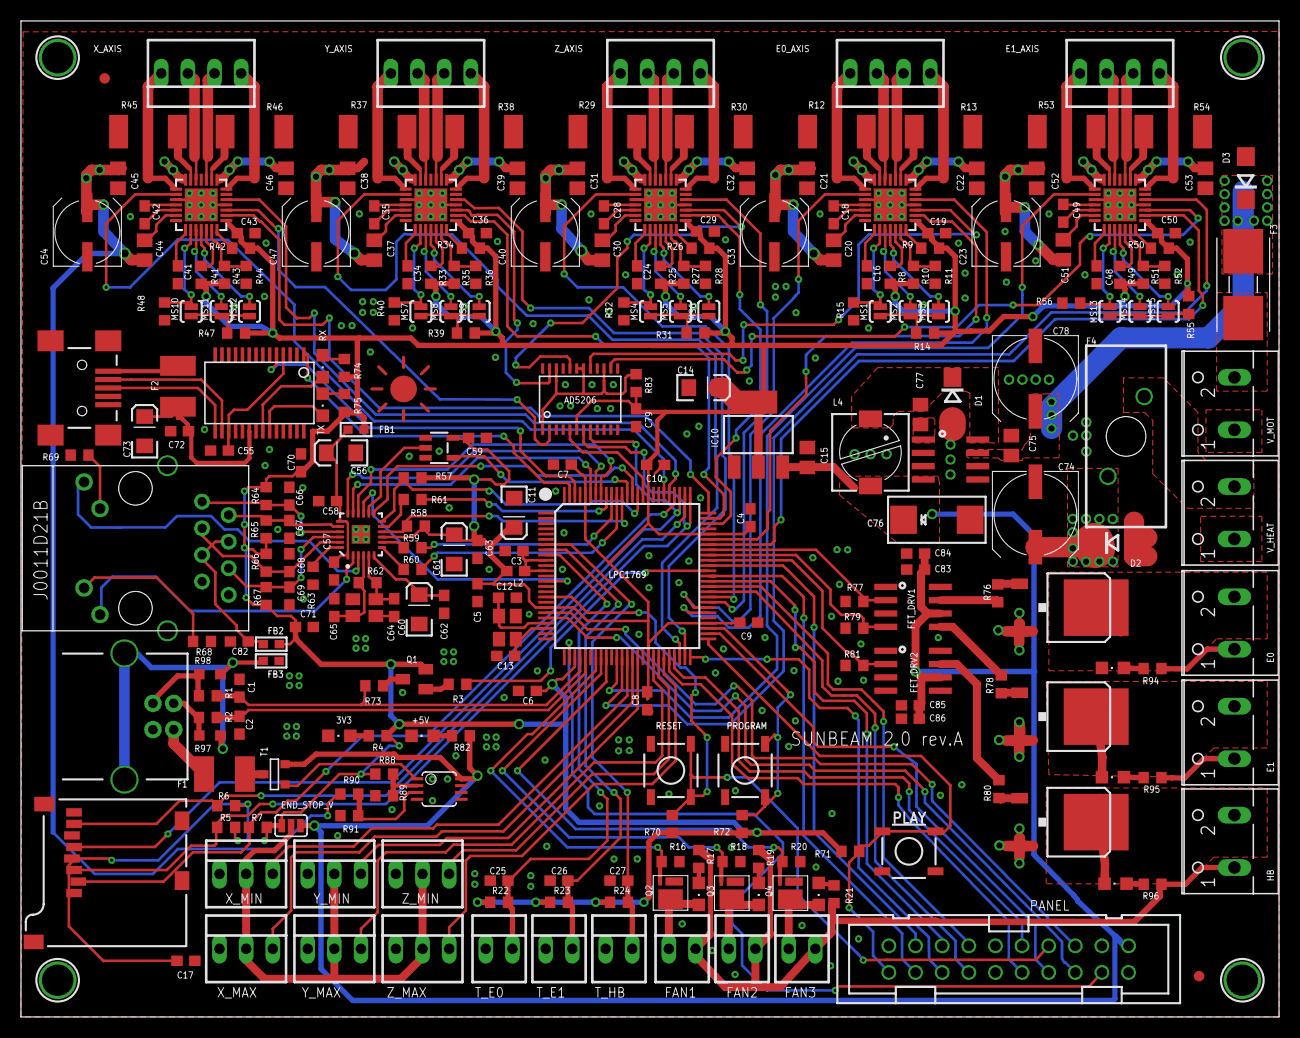
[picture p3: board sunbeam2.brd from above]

Board: 2 copper layers, 120.0 x 95.0 mm, 276 parts (0 on the bottom side), 227 nets.

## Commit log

2013-01-05 -changed 3 2 channel pots to one 6 channel -moved play button -added fet driver for heater instead of bjts -changed some polygons [thanks triffin_hunter]
    [sunbeam2.brd, sunbeam2.sch]
2013-01-09 -changed heaters fuse -some slight component changes
    [sunbeam2.brd, sunbeam2.sch]
2013-01-09 -first BOM
    [bom_table.xls]
2013-01-10 nothing important
    [sunbeam2.brd]
2013-01-30 added paste layer for tranzistors
    [sunbeam2.brd, sunbeam2.sch]

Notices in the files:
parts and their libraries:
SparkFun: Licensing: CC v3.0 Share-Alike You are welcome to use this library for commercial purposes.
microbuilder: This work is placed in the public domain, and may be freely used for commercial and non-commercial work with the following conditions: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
